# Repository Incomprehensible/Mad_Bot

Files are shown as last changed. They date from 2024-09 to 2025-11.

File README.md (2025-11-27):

# Mad_Bot
Exploratory project in Embedded Robotics and Swarm Algorithms

Warning: This is an ongoing project, and the repository is under construction!

## Features
* Small PCB-based frame, minimum 3D printed parts
* ESP32-S3 MCU with vector instructions, acceleration for neural network computing and signal processing workloads
* Wi-Fi, Bluetooth 5 and BLE connectivity
* Omnidirectional movement
* Quadrature encoders for precise movement
* 8 MB PSRAM for image processing
* 2 Megapixel camera and ToF sensors for running embedded robotics algorithms
* Powered via USB-C or 3000mAh LiPo battery with inner protection and external charging circuit
* Load sharing circuit for operating the robot while charging
* Buck-Boost converter for powering the MCU and peripherals
* 6V regulator for powering the middle power range motors
* ESPNOW, ESP-WIFI-MESH or ESP-BLE-MESH for communication between several robots
* Integrated MEMS microphone for sound recognition
* micro-ROS support

**Note**: Software support for some features is still in progress.

## Fusion360 design
| | |
|---|---|
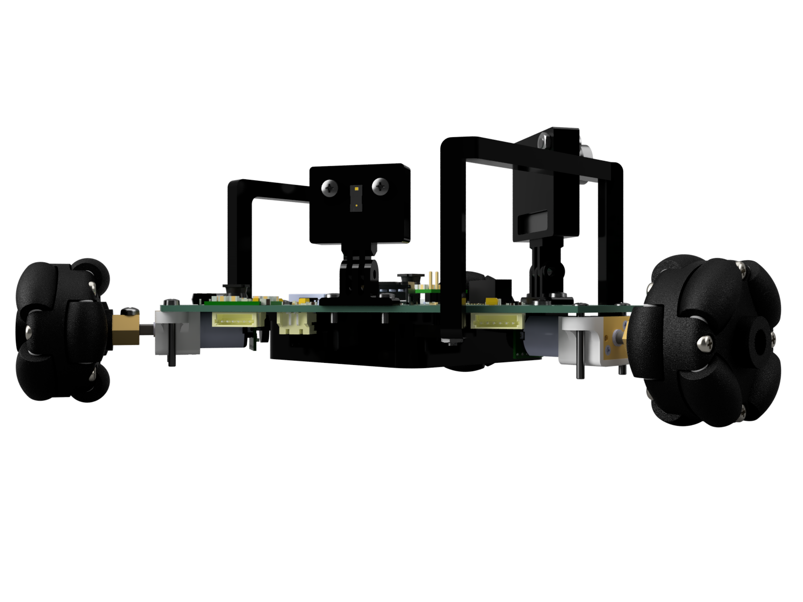
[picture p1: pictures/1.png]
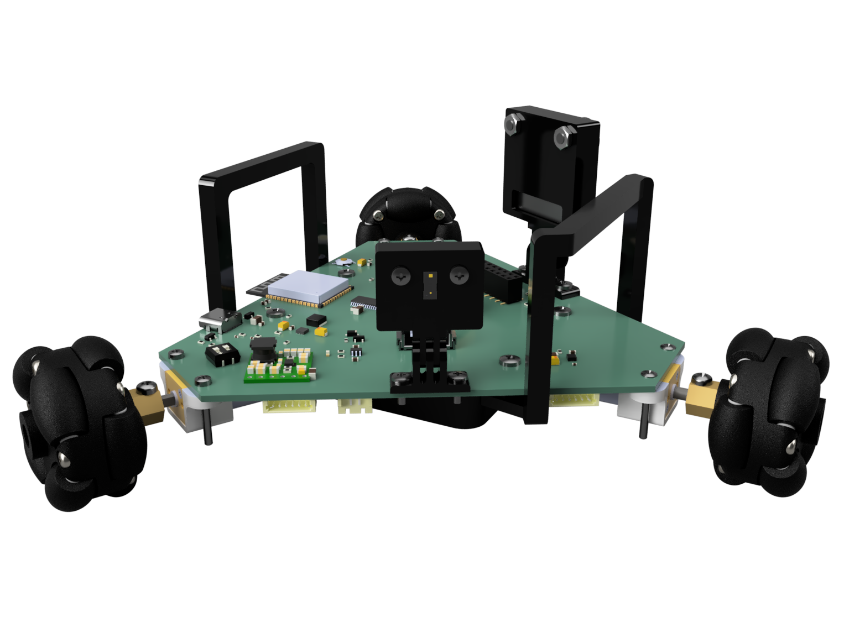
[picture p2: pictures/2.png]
|  |  |
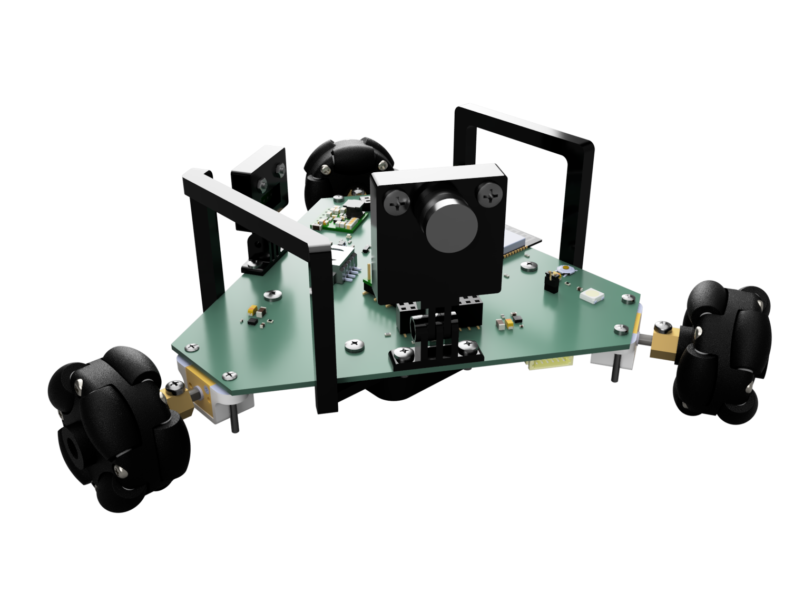
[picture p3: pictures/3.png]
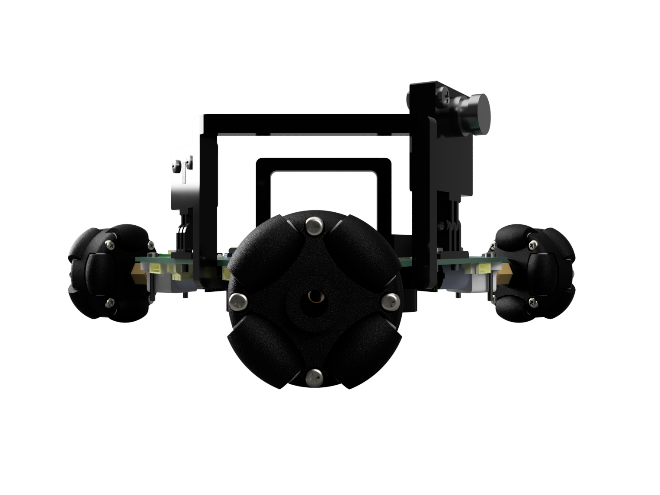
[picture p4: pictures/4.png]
|  |  |

## URDF model
<details>

| Robot | Wheel |
|---|---|
|  |  |

</details>

## Operation demo
<details>

| Forward movement | Backward movement | Rotation |
|:---:|:---:|:---:|
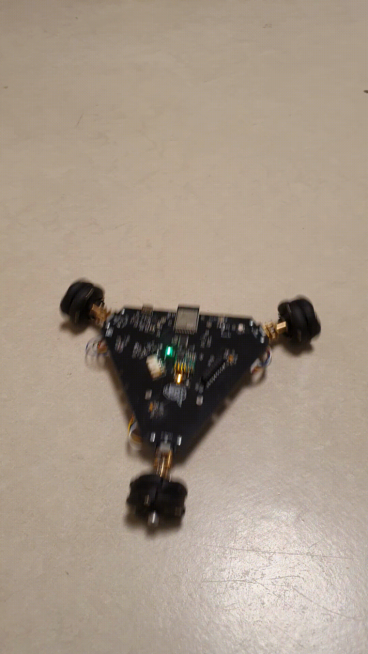
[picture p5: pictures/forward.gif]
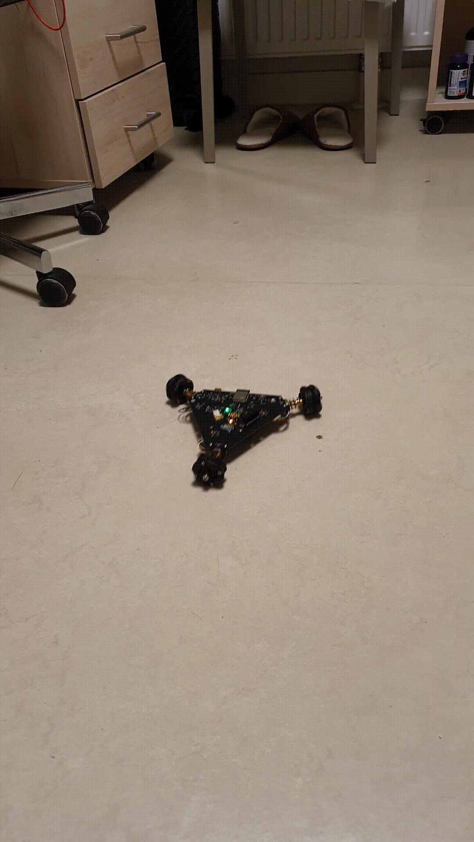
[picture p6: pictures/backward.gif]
|  |  |  |
<!-- | ![Forward movement](pictures/forward.gif) | ![Backward movement](pictures/backward.gif) | ![Rotation](pictures/twist.gif) | -->

</details>

### Charging mode
<details>
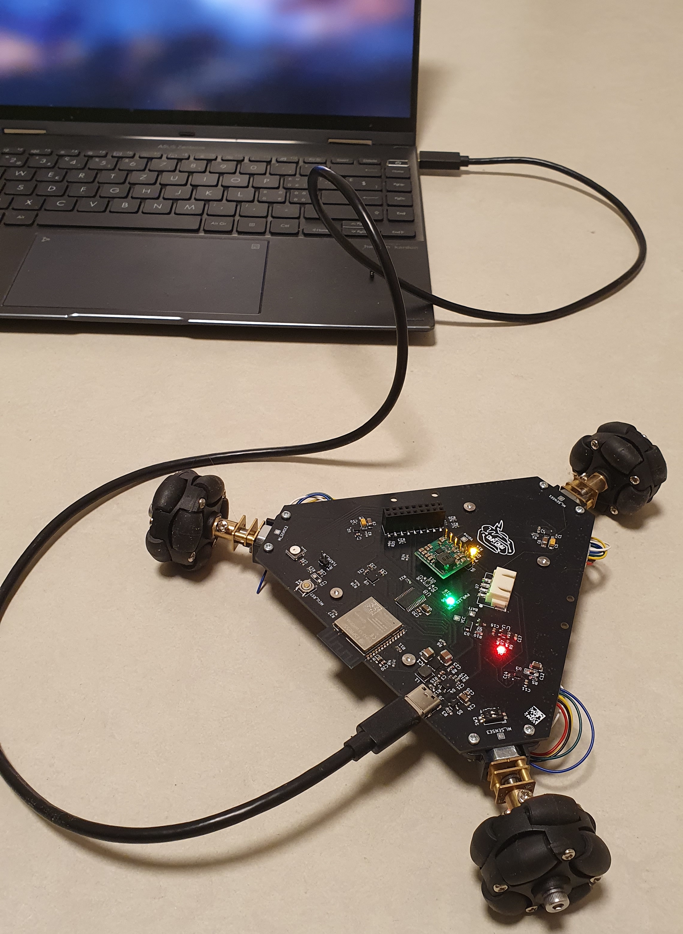
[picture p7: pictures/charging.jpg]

</details>

## Board layout
<details>

</details>

## Future work
- [ ] Add a BOM
- [X] Design a carrier extension in Fusion360
- [X] Test battery charging circuit
- [X] Test load sharing circuit
- [X] Test basic functionality with motors and ESP32-S3
- [X] Test Wi-Fi
- [X] Motors library (in progress)
- [X] Encoders testing
- [ ] **Device firmware (in progress)**
- [ ] **Sensors testing (in progress)**:
  - [ ] Camera
  - [X] ToF
  - [X] IMU
  - [ ] *MEMS microphone (requires PCB bug fix)*
- [ ] Remote controller based on ESP32
- [ ] PSRAM memory testing
- [X] **ROS2 integration via micro-ROS (in progress)**
- [ ] Web page with control interface and telemetry
- [X] URDF model
- [X] Joystick control via ROS2
- [ ] Digital twin for simulation in Gazebo and Mujoco
- [ ] ESPNOW and Mesh experiments
- [ ] Multi-agent algorithms
- [ ] Computer vision algorithms
- [ ] Mini SLAM experiments

## Fix list for new hardware revisions
* MEMS microphone footprint flipped
* Non-fixed Buck-Boost mentioned in the schematics instead of 3.3V fixed
* 6V regulator doesn't disconnect the load if disabled because of topology - extra switch needed
* Battery connector is hard to remove - source power switch needed
* Better (aligned) placement for camera & ToF sensors

## Software Troubleshooting

### micro-ROS build issues
If you encounter issue like [this](https://github.com/micro-ROS/micro_ros_espidf_component/issues/251) building micro-ROS for the ESP32-S3 platform, edit [`libmicroros.mk`](https://github.com/micro-ROS/micro_ros_espidf_component/blob/humble/libmicroros.mk) file at line 110 to include `esp32s3` as follows:

```makefile
ifeq ($(IDF_TARGET),$(filter $(IDF_TARGET),esp32s2 esp32c3 esp32c6 esp32s3))
```

## Acknowledgements
This project takes inspiration from the following open-source projects:
* https://github.com/YePeOn7/ros2_omni_robot_sim (omnidirectional drive kinematics)
* https://github.com/twistx77/V53L7CX-Library.git (ToF sensor library)
* https://github.com/natanaeljr/esp32-mpu-driver (IMU driver)
* Jonas Scharpf code pf the PCA9685 driver (motor PWM driver)

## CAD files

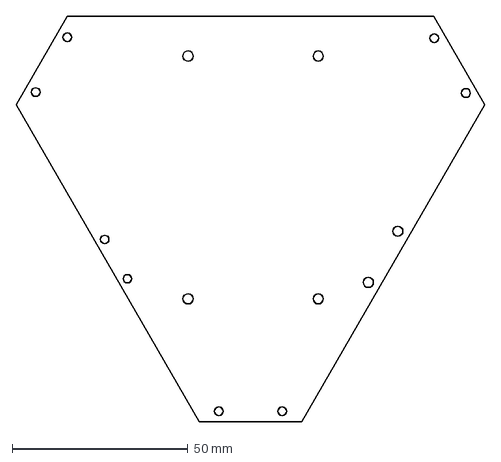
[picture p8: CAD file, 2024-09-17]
pcb_design/Board Outline.dxf
133.1 x 115.3 mm

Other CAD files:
3d_models/ESP32-S3-WROOM-1-N8R8.step
fusion360/PCB.step
urdf/meshes/roller2.stl
3d_models/step-up-voltage-regulator-u3v40fx.step
fusion360/Mad_Bot.step
urdf/meshes/wheel_fixture2-2.stl
3d_models/IC12_MP6550_MNP.step
urdf/meshes/roller1-1.stl
3d_models/QFN24_3X3X0P9_MPU6500.step
urdf/meshes/root1.stl
3d_models/PCA9685PW_118.step
urdf/meshes/roller6.stl
3d_models/TYPE-C-31-M-12.step
urdf/meshes/roller5-1.stl
3d_models/MPU-6500.step
urdf/meshes/Component42.stl
3d_models/TYPE-C-31-M-12-ver2.step
3d_models/AO3400A--3DModel-STEP-269445.STEP
3d_models/HRO_TYPE-C-31-M-12.step
3d_models/Jumper-2mm-h3.5.STEP
3d_models/MCP73831T-2ACI_OT.step
3d_models/PTS526_SK15_SMTR2_LFS.stp
3d_models/RT6150BGQW.stp
3d_models/S2B-PH-SM4-TB_LF__SN_.step
3d_models/S4B-XH-SM4-TB-LF--SN---3DModel-STEP-56544.STEP
3d_models/S6B-ZR-SM4A-TF_1.5mm.step
3d_models/WS2812B.step
fusion360/Mad_Bot.f3z
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

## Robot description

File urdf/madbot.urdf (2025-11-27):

<?xml version='1.0' encoding='utf-8'?>
<robot name="madbot">
    <link name="roller8">
        <inertial>
            <origin xyz="1.0439394522909762e-06 -1.4014728133560085e-09 4.298914557665512e-09" rpy="0.0 -0.0 0.0" />
            <mass value="0.007815431237643264" />
            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
        </inertial>
        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
    </link>
    <link name="root1">
        <inertial>
            <origin xyz="-3.100341341877311e-08 -1.1752218942007176e-07 1.1202703679824566e-07" rpy="0.0 1.5407439555097882e-33 0.0" />
            <mass value="0.0004307740437553794" />
            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
        </inertial>
        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
    </link>
    <link name="roller2">
        <inertial>
            <origin xyz="7.104420888293106e-07 7.407909580248173e-07 1.9459895433726615e-07" rpy="0.0 -1.8662408846864425e-43 0.0" />
            <mass value="0.007815431237643047" />
            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
        </inertial>
        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
    </link>
    <link name="stem1">
        <inertial>
            <origin xyz="1.8899693657381533e-06 7.304546818021063e-06 -7.0571409794828455e-06" rpy="0.0 1.540743955510633e-33 0.0" />
            <mass value="0.0011510552143977049" />
            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
        </inertial>
        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
    </link>
    <link name="roller1">
        <inertial>
            <origin xyz="-1.905487767572822e-07 -7.385234957646425e-07 7.177578375516803e-07" rpy="0.0 -2.77207726435891e-43 1.4349296274686127e-42" />
            <mass value="0.007815431237643685" />
            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
        </inertial>
        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
    </link>
    <link name="stem2">
        <inertial>
            <origin xyz="-7.057385601761945e-06 -7.3022794153221325e-06 -1.8929902407727184e-06" rpy="0.0 -1.5407439555079787e-33 -6.162975822039155e-33" />
            <mass value="0.0011510552143976025" />
            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
        </inertial>
        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
    </link>
    <link name="root3">
        <inertial>
            <origin xyz="2.71807154028636e-08 -1.1371580499686118e-07 1.1118542941224164e-07" rpy="0.0 -1.5407439555097882e-33 -6.162975822039155e-33" />
            <mass value="0.00043077404375536606" />
            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
        </inertial>
        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
    </link>
    <link name="root4">
        <inertial>
            <origin xyz="-1.1801200489269803e-07 1.1359585382231252e-07 3.123094604262633e-08" rpy="0.0 1.5407439555097883e-33 0.0" />
            <mass value="0.00043077404375537924" />
            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
        </inertial>
        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
    </link>
    <link name="stem5">
        <inertial>
            <origin xyz="-5.165218458689225e-06 1.4776153689499694e-09 8.945080346620672e-06" rpy="0.0 -0.0 0.0" />
            <mass value="0.001151055214397071" />
            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
        </inertial>
        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
    </link>
    <link name="roller5">
        <inertial>
            <origin xyz="-3.137685427709869e-06 1.477901773183632e-09 5.437748869319137e-06" rpy="0.0 -0.0 0.0" />
            <mass value="0.00781543123764419" />
            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
        </inertial>
        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
    </link>
    <link name="Component14">
        <inertial>
            <origin xyz="0.0002571060522190471 0.00014897032367631625 -5.603945090504325e-07" rpy="0.0 -0.0 0.0" />
            <mass value="0.0004109447446555896" />
            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
        </inertial>
        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
    </link>
    <link name="Component15">
        <inertial>
            <origin xyz="0.0002571112578287682 0.00014897302145918444 -5.590028332258523e-07" rpy="0.0 -0.0 0.0" />
            <mass value="0.00041094474463731237" />
            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
        </inertial>
        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
    </link>
    <link name="roller7">
        <inertial>
            <origin xyz="-5.219318596960676e-07 1.4772004419683072e-09 -9.074879243442524e-07" rpy="0.0 8.758115402067066e-47 0.0" />
            <mass value="0.007815431237643496" />
            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
        </inertial>
        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
    </link>
    <link name="Component17">
        <inertial>
            <origin xyz="0.00025706019450405293 0.00014905965433701596 4.6687570287029526e-07" rpy="0.0 -0.0 0.0" />
            <mass value="0.00041094474463718855" />
            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
        </inertial>
        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
    </link>
    <link name="roller6">
        <inertial>
            <origin xyz="-1.0439387513150322e-06 -3.405877295747928e-09 4.2235343933327844e-09" rpy="4.307493387644509e-59 -0.0 0.0" />
            <mass value="0.007815431237643378" />
            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
        </inertial>
        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
    </link>
    <link name="stem6">
        <inertial>
            <origin xyz="-1.4214342886342823e-06 -3.40612094085202e-09 4.2236750541491124e-09" rpy="4.307493387644509e-59 -0.0 0.0" />
            <mass value="0.0011510552143977034" />
            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
        </inertial>
        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
    </link>
    <link name="root2">
        <inertial>
            <origin xyz="1.1178253624954949e-07 1.197894636328911e-07 2.7982571122464605e-08" rpy="0.0 -1.5407439555097883e-33 0.0" />
            <mass value="0.00043077404375539203" />
            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
        </inertial>
        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
    </link>
    <link name="roller4">
        <inertial>
            <origin xyz="-7.096004910112086e-07 7.345973547984164e-07 1.9077625985630677e-07" rpy="0.0 -1.600695501510992e-51 0.0" />
            <mass value="0.007815431237643463" />
            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
        </inertial>
        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
    </link>
    <link name="stem7">
        <inertial>
            <origin xyz="-7.106796283640193e-07 1.476918787268744e-09 -1.2344086490578832e-06" rpy="0.0 8.758115402067066e-47 0.0" />
            <mass value="0.0011510552143978619" />
            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
        </inertial>
        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
    </link>
    <link name="stem4">
        <inertial>
            <origin xyz="7.051156133495162e-06 -7.308473026466089e-06 -1.8897418681795843e-06" rpy="0.0 1.5407439555101537e-33 -6.162975822039155e-33" />
            <mass value="0.0011510552143976602" />
            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
        </inertial>
        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
    </link>
    <link name="root7">
        <inertial>
            <origin xyz="-8.290144054790005e-08 1.476955353574283e-09 -1.4706493130844934e-07" rpy="0.0 -0.0 0.0" />
            <mass value="0.0004307740437555343" />
            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
        </inertial>
        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
    </link>
    <link name="roller3">
        <inertial>
            <origin xyz="1.937971468102262e-07 -7.347171158672561e-07 7.09845161466216e-07" rpy="0.0 -4.3302330459644565e-45 0.0" />
            <mass value="0.007815431237643299" />
            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
        </inertial>
        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
    </link>
    <link name="root5">
        <inertial>
            <origin xyz="8.297682004609897e-08 1.4776574397412645e-09 -1.4506052782081723e-07" rpy="0.0 -0.0 0.0" />
            <mass value="0.00043077404375551774" />
            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
        </inertial>
        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
    </link>
    <link name="stem3">
        <inertial>
            <origin xyz="-1.893792061284927e-06 7.308353204705797e-06 -7.057982583879019e-06" rpy="1.751623080406021e-46 6.211560498438912e-60 -7.006492321624084e-46" />
            <mass value="0.0011510552143976153" />
            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
        </inertial>
        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
    </link>
    <link name="root6">
        <inertial>
            <origin xyz="-1.6587791243027894e-07 -3.406091675373091e-09 4.223658214286274e-09" rpy="-3.038581678643135e-64 -0.0 0.0" />
            <mass value="0.0004307740437553726" />
            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
        </inertial>
        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
    </link>
    <link name="Component29">
        <inertial>
            <origin xyz="-0.002595641529595074 0.0014985139369473545 -7.228449571705653e-07" rpy="0.0 -0.0 0.0" />
            <mass value="0.0004109447446236162" />
            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
        </inertial>
        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
    </link>
    <link name="Component30">
        <inertial>
            <origin xyz="-0.00025770289094363187 0.00014795231939298325 6.769750041046851e-08" rpy="0.0 -0.0 0.0" />
            <mass value="0.000410944743236442" />
            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
        </inertial>
        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
    </link>
    <link name="Component31">
        <inertial>
            <origin xyz="0.0002576191973983555 0.000148093341563591 -4.6687677290657703e-07" rpy="0.0 -0.0 0.0" />
            <mass value="0.00041094474465542847" />
            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
        </inertial>
        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
    </link>
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

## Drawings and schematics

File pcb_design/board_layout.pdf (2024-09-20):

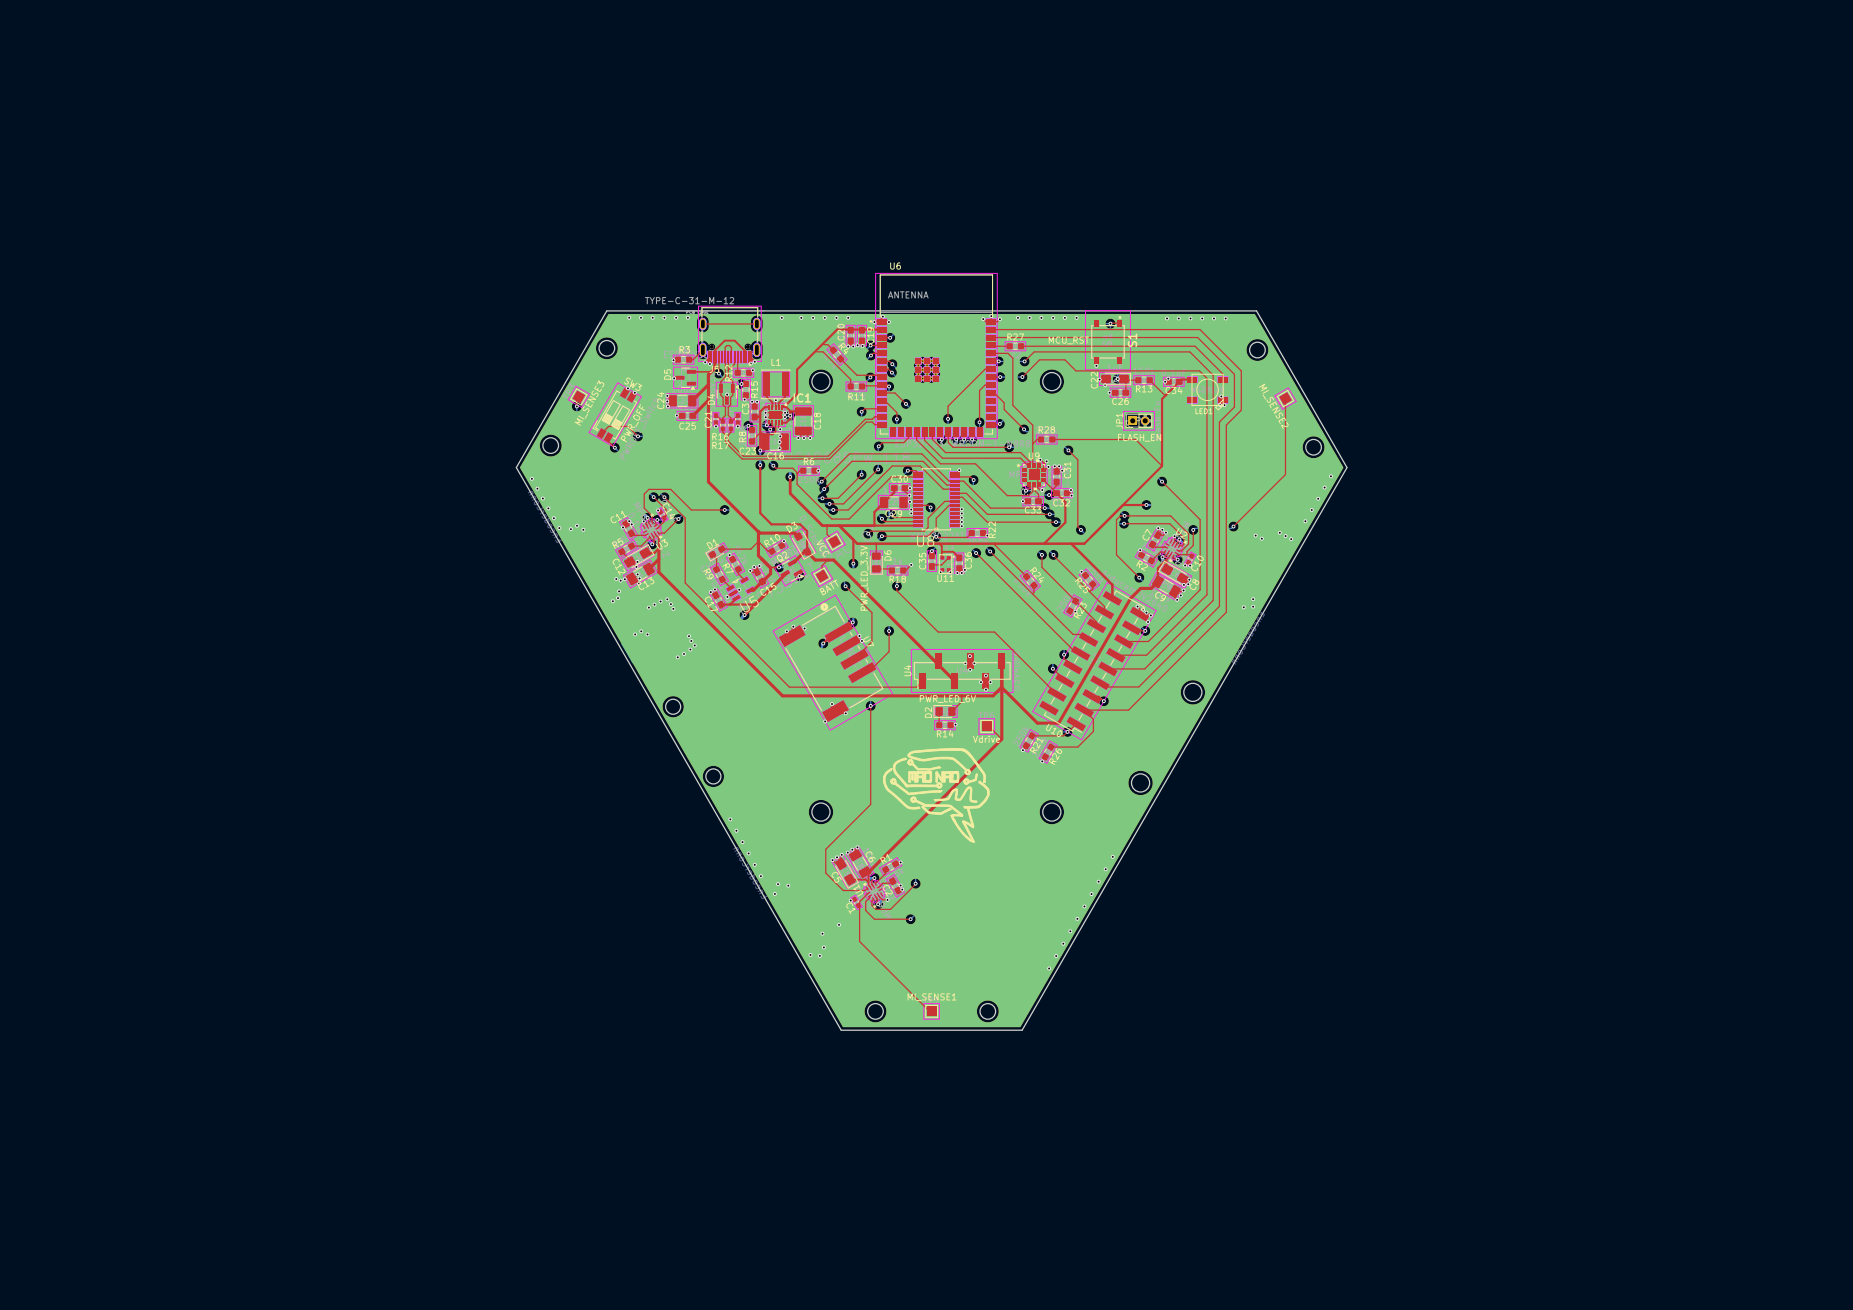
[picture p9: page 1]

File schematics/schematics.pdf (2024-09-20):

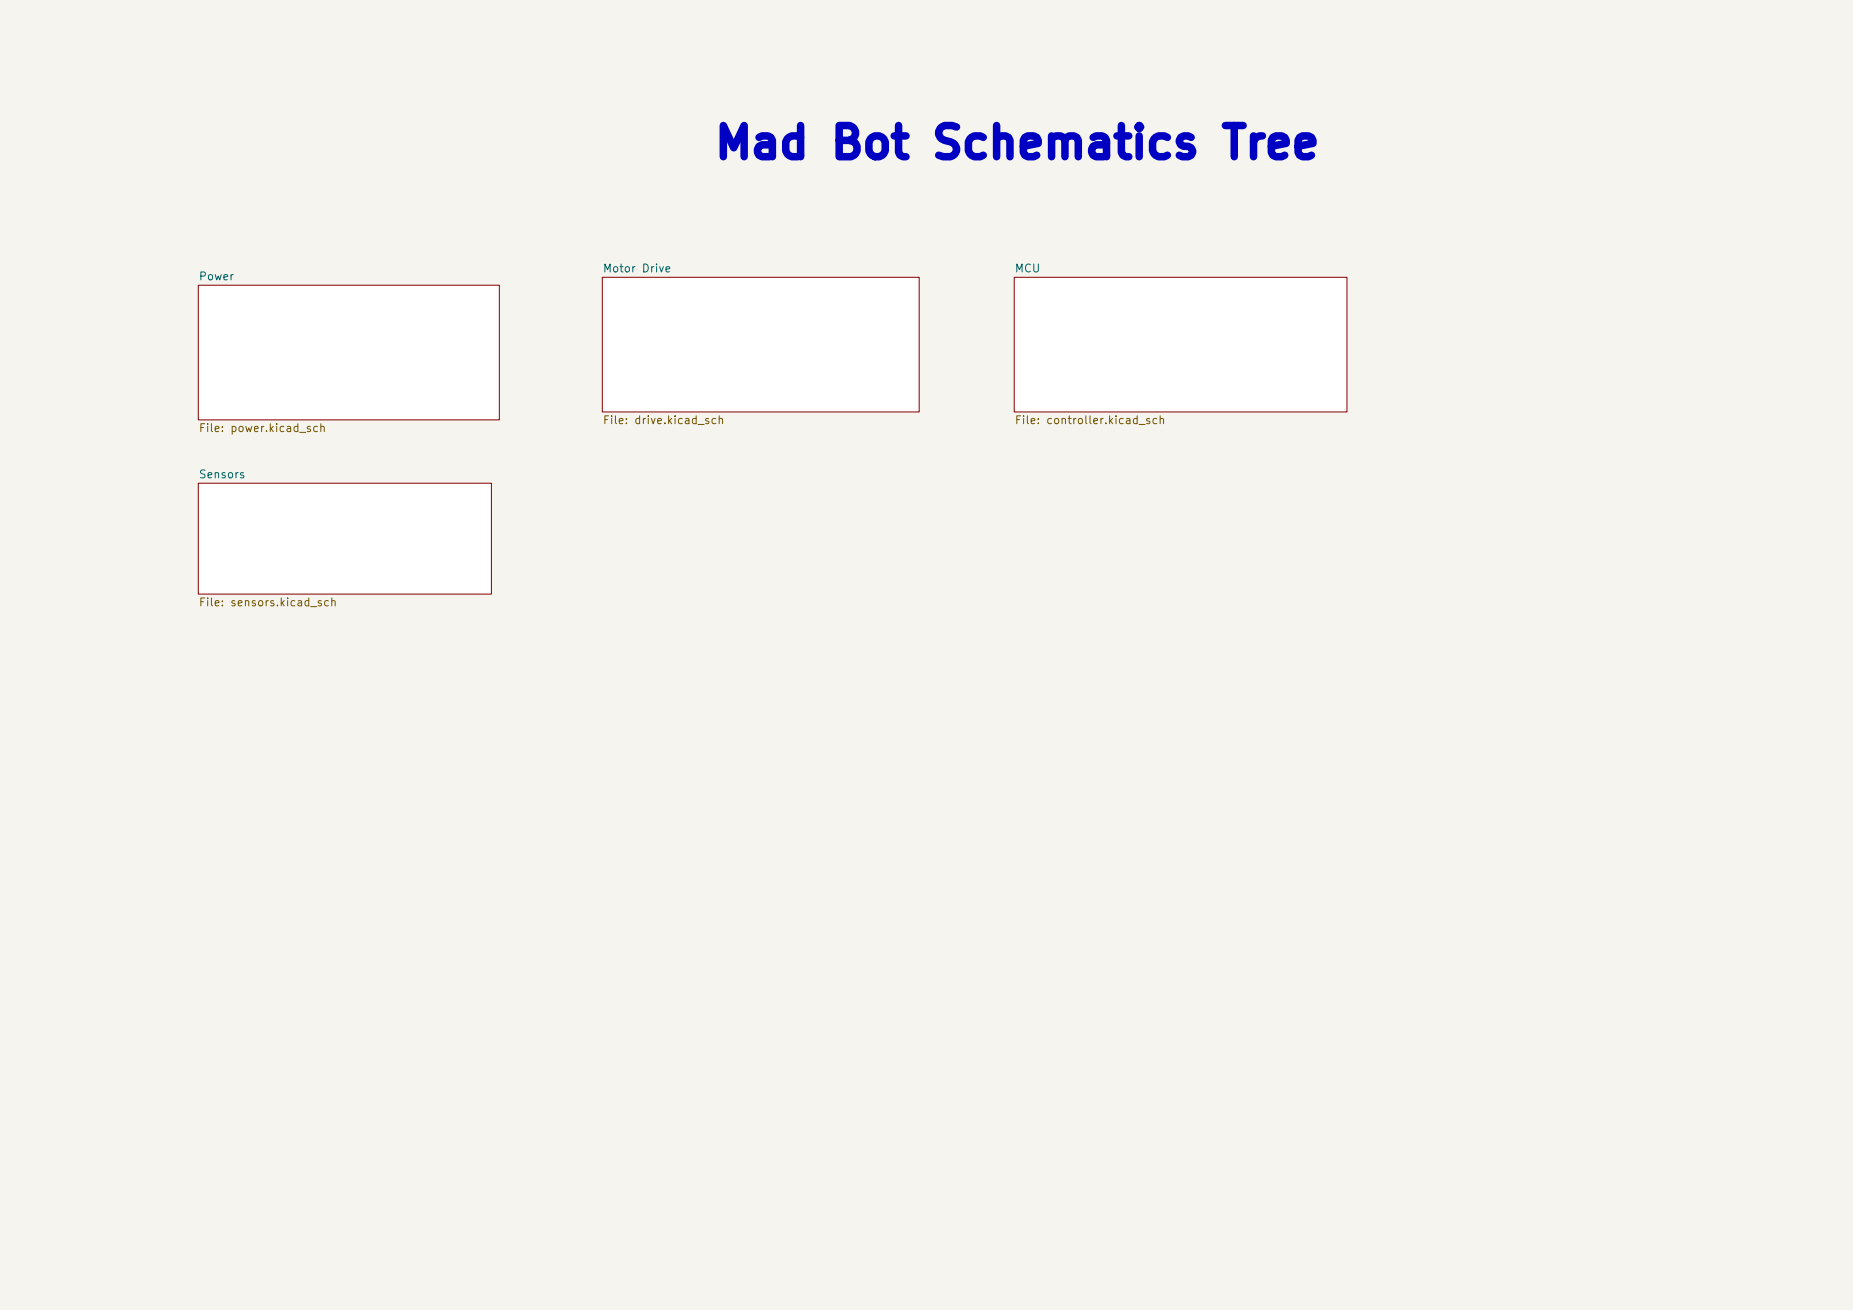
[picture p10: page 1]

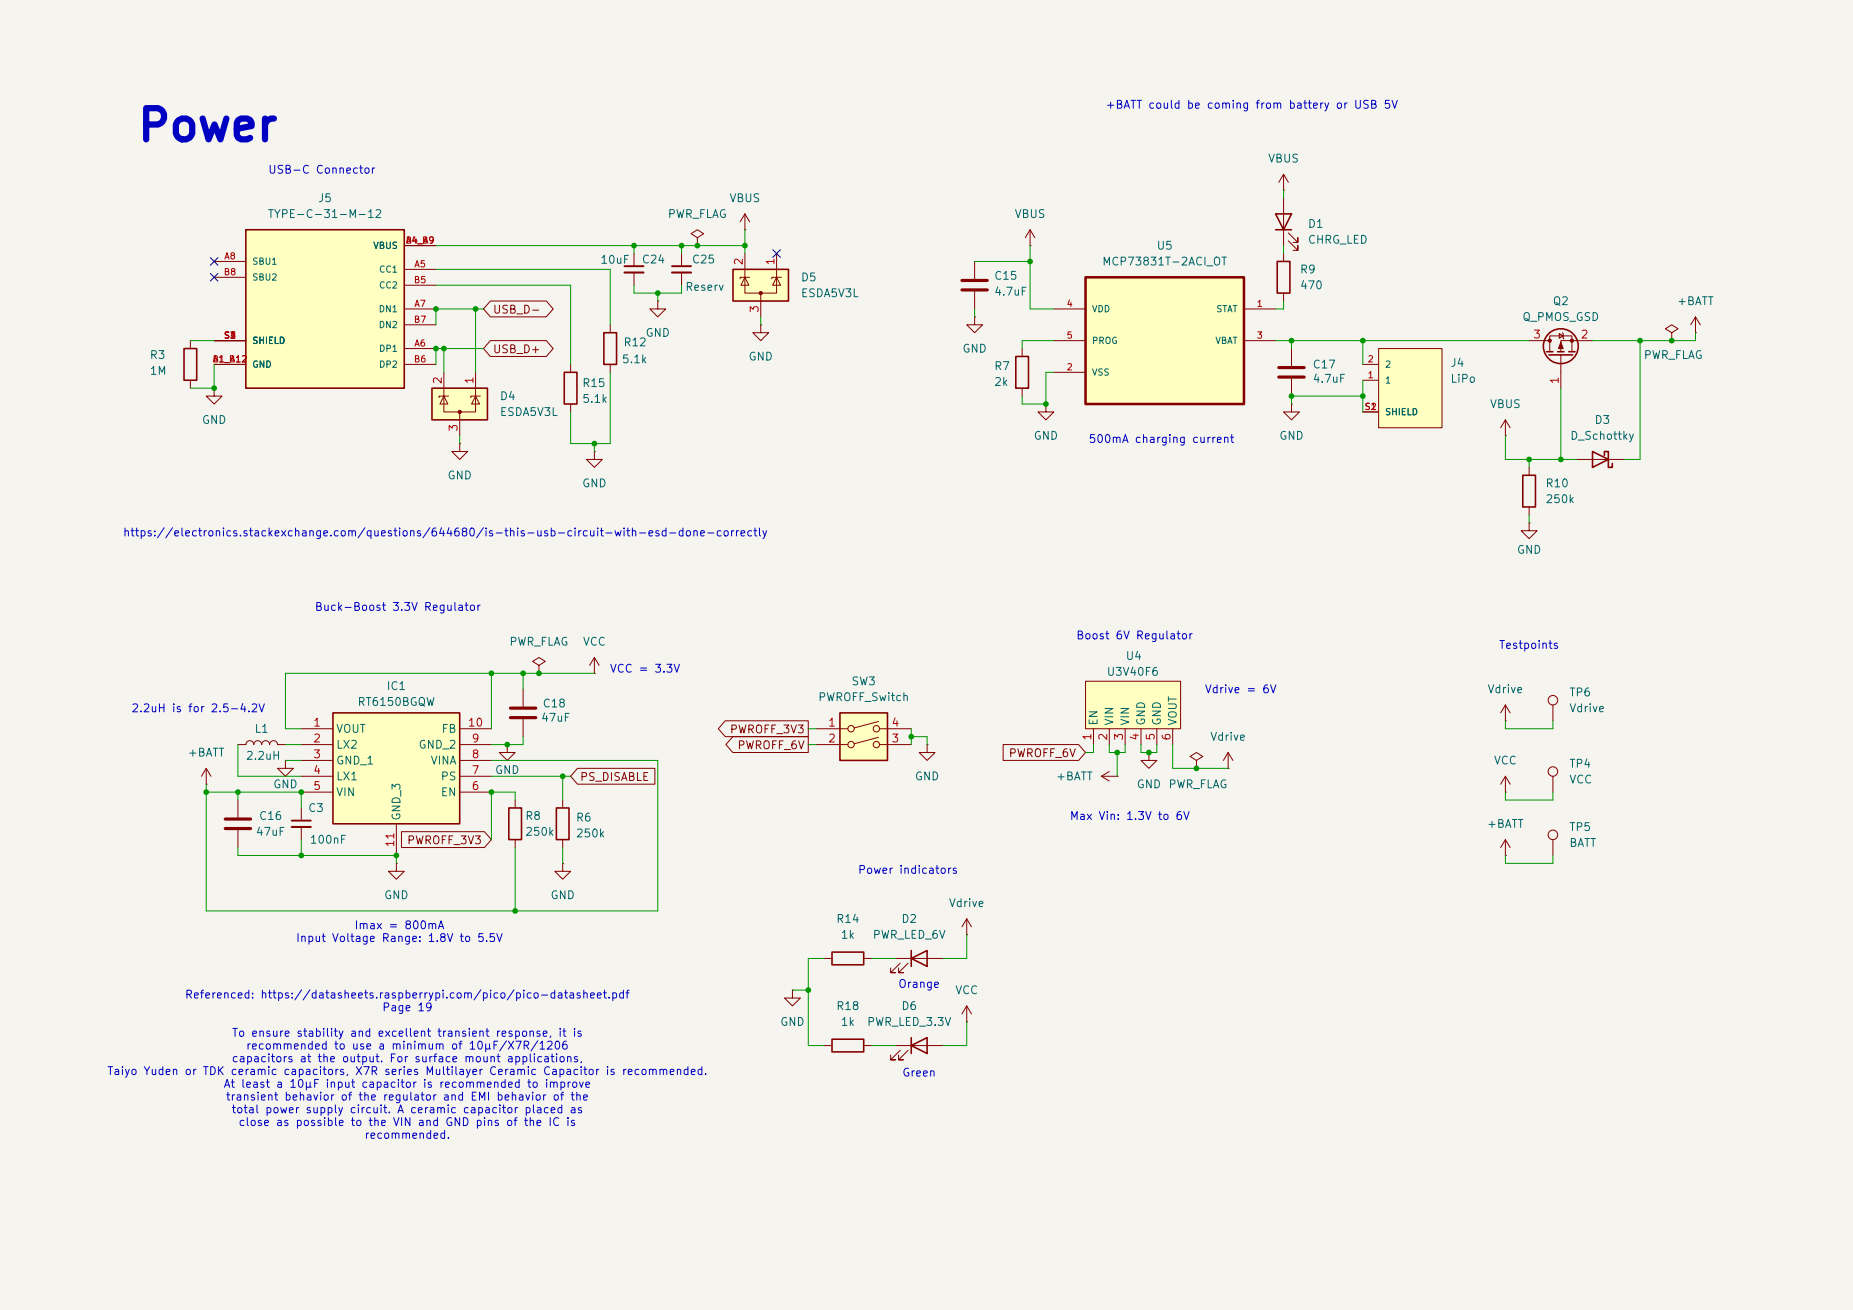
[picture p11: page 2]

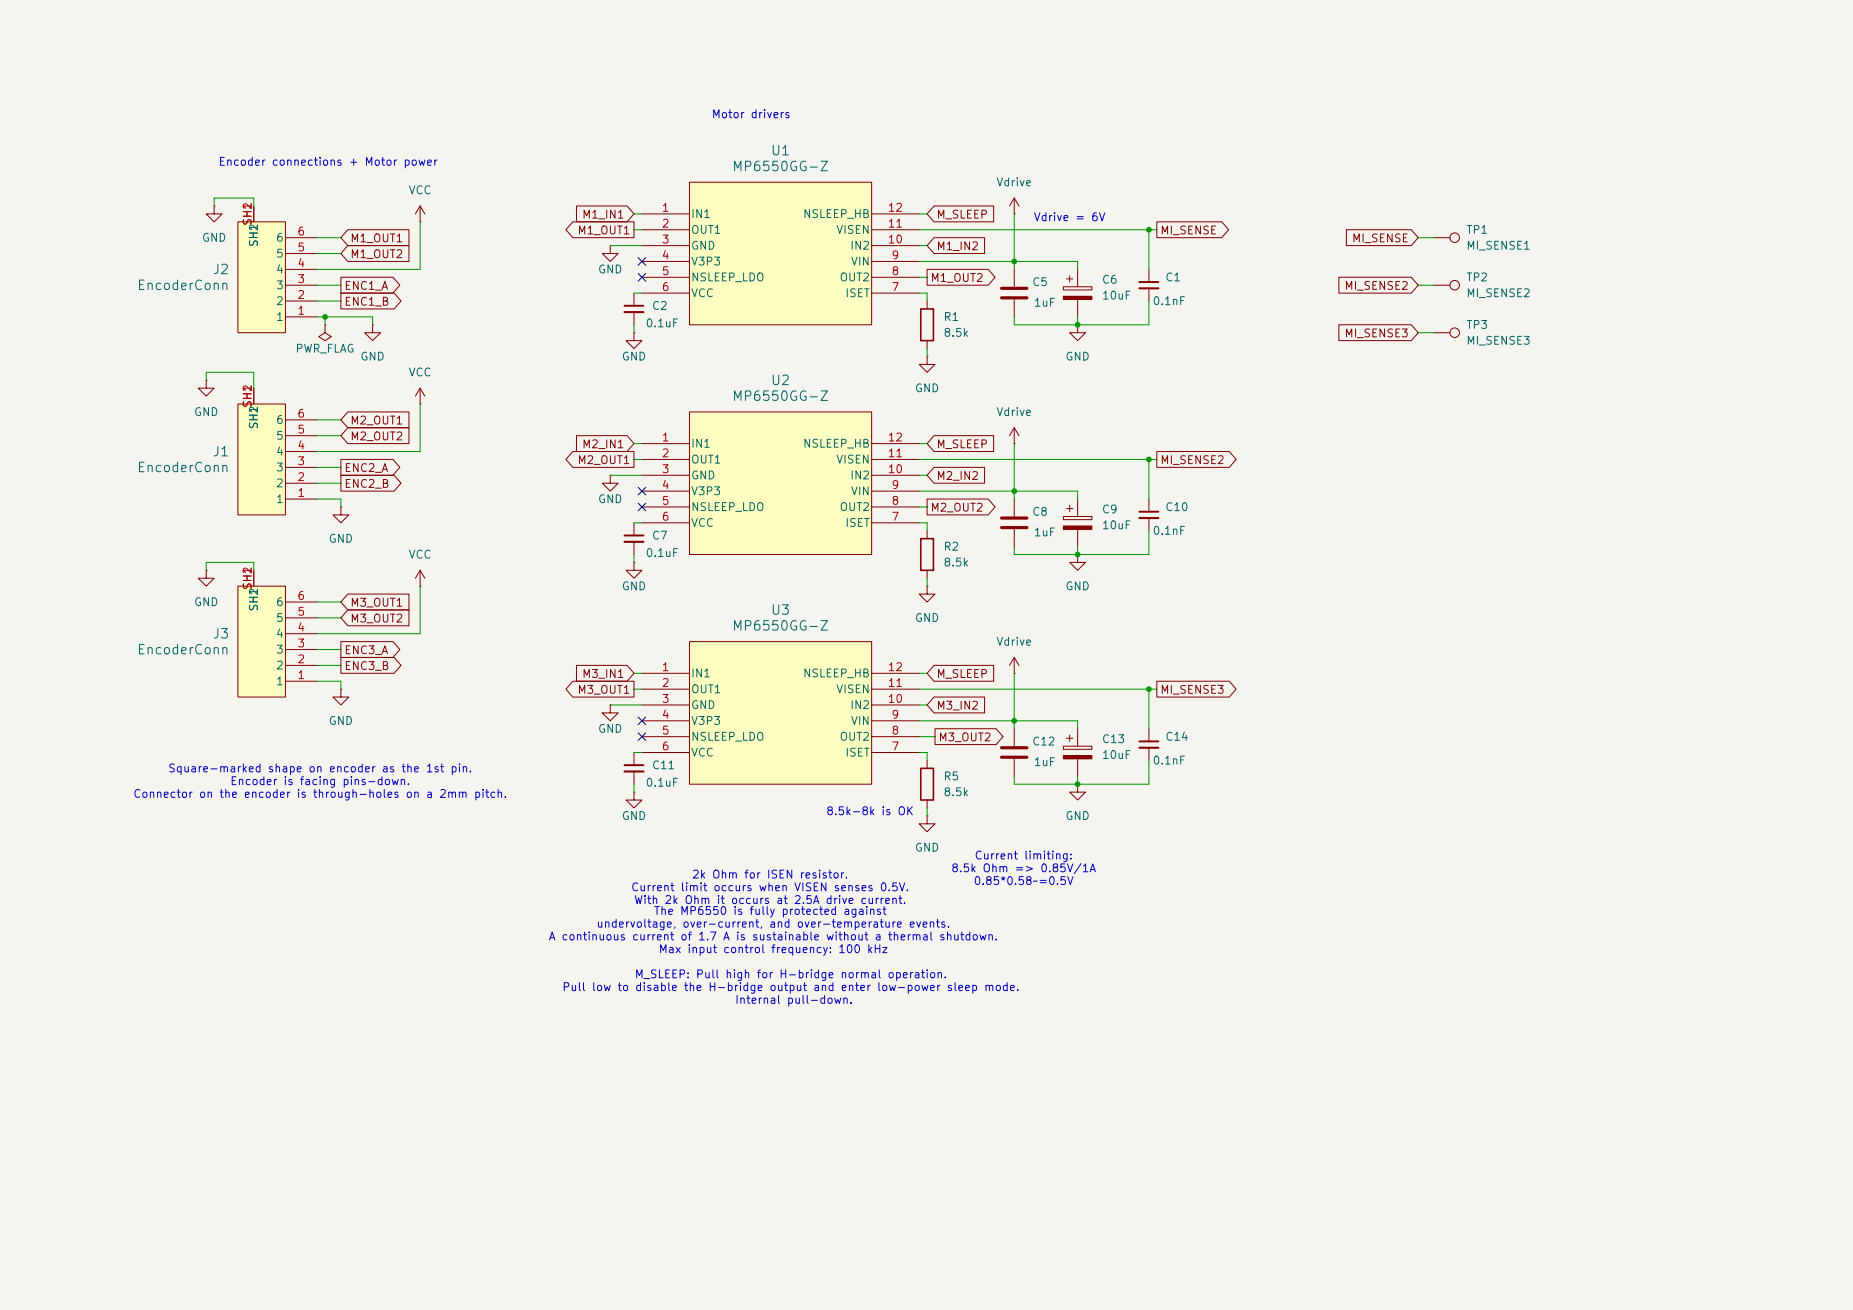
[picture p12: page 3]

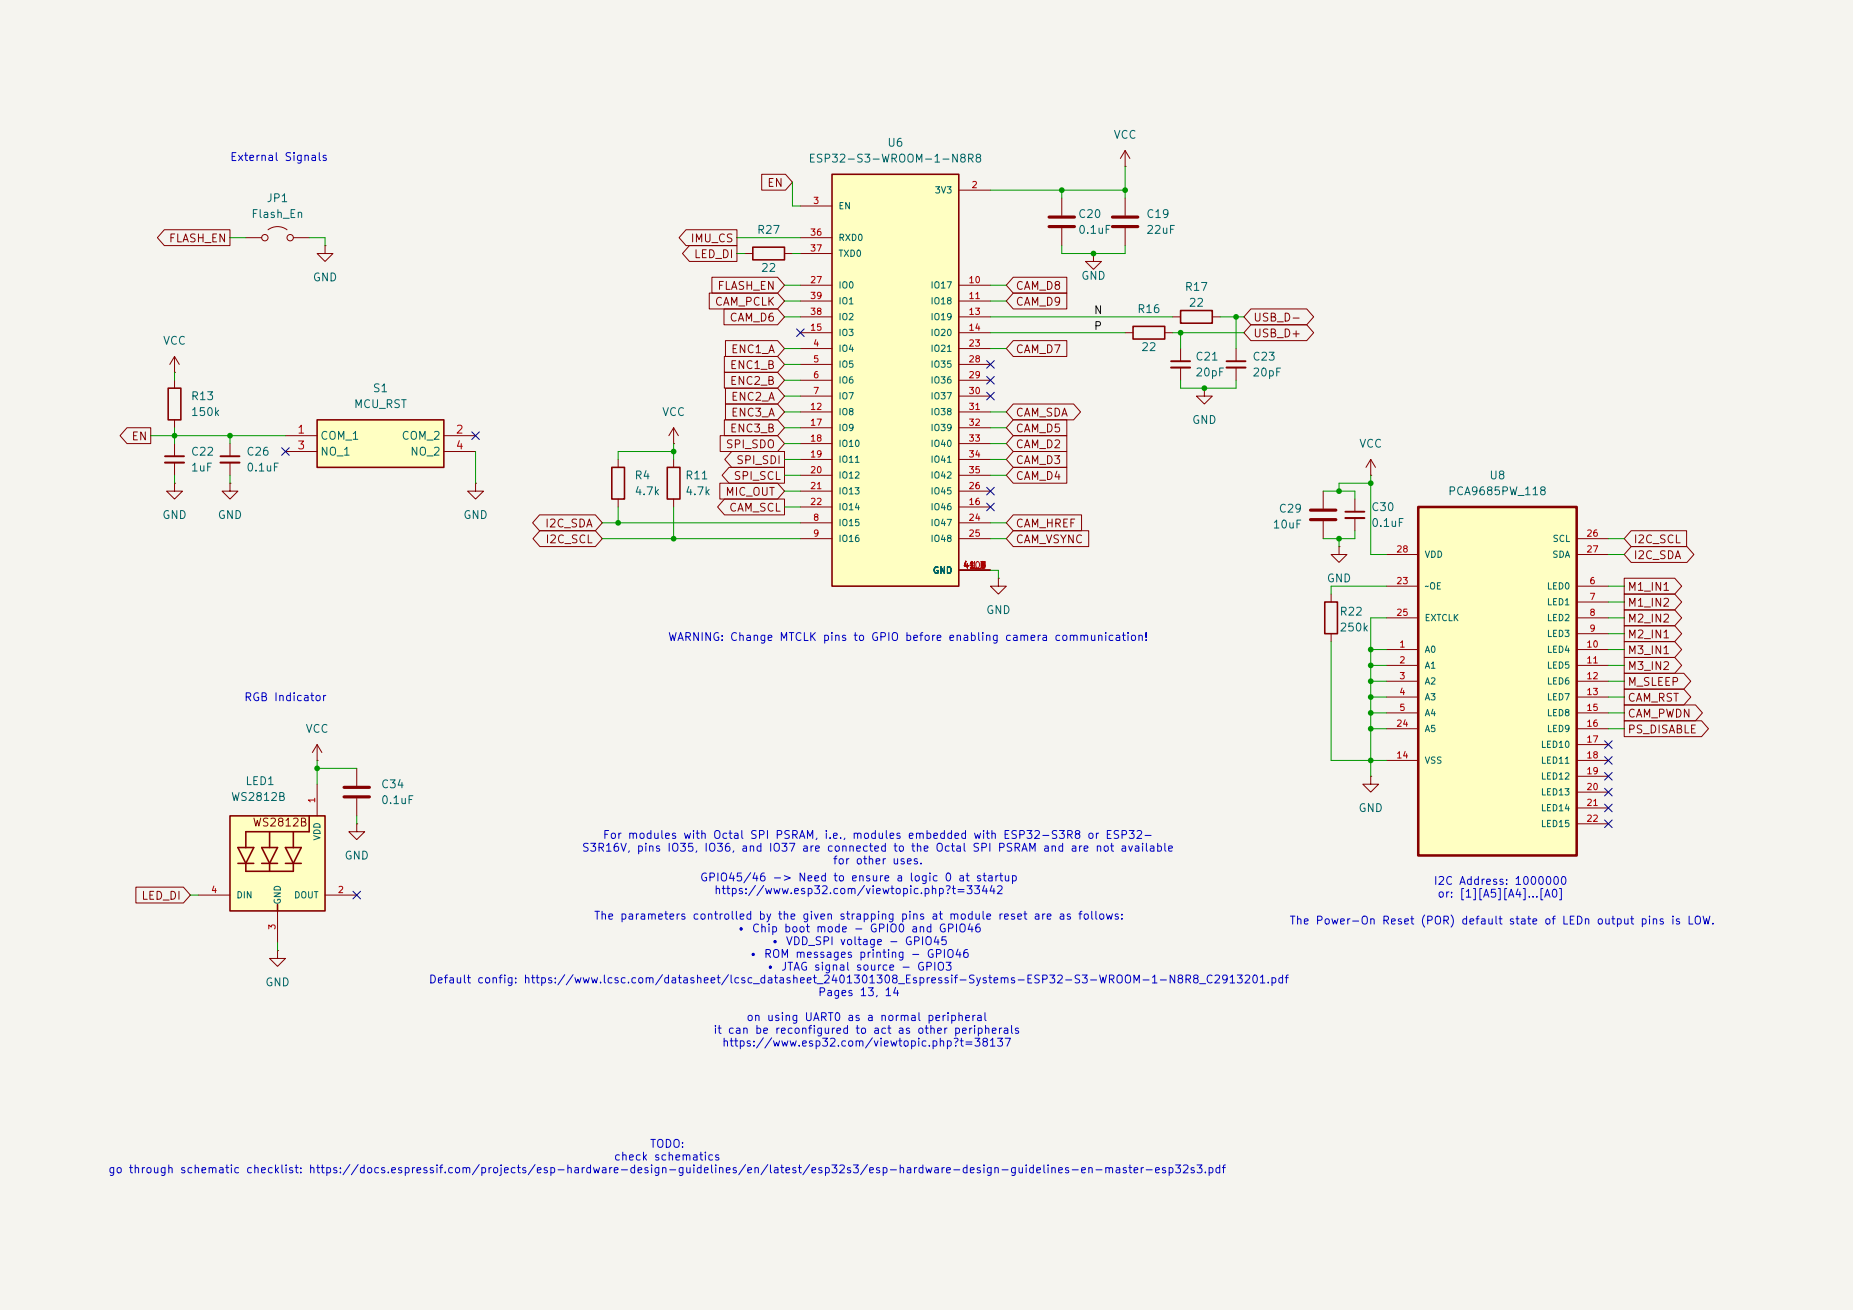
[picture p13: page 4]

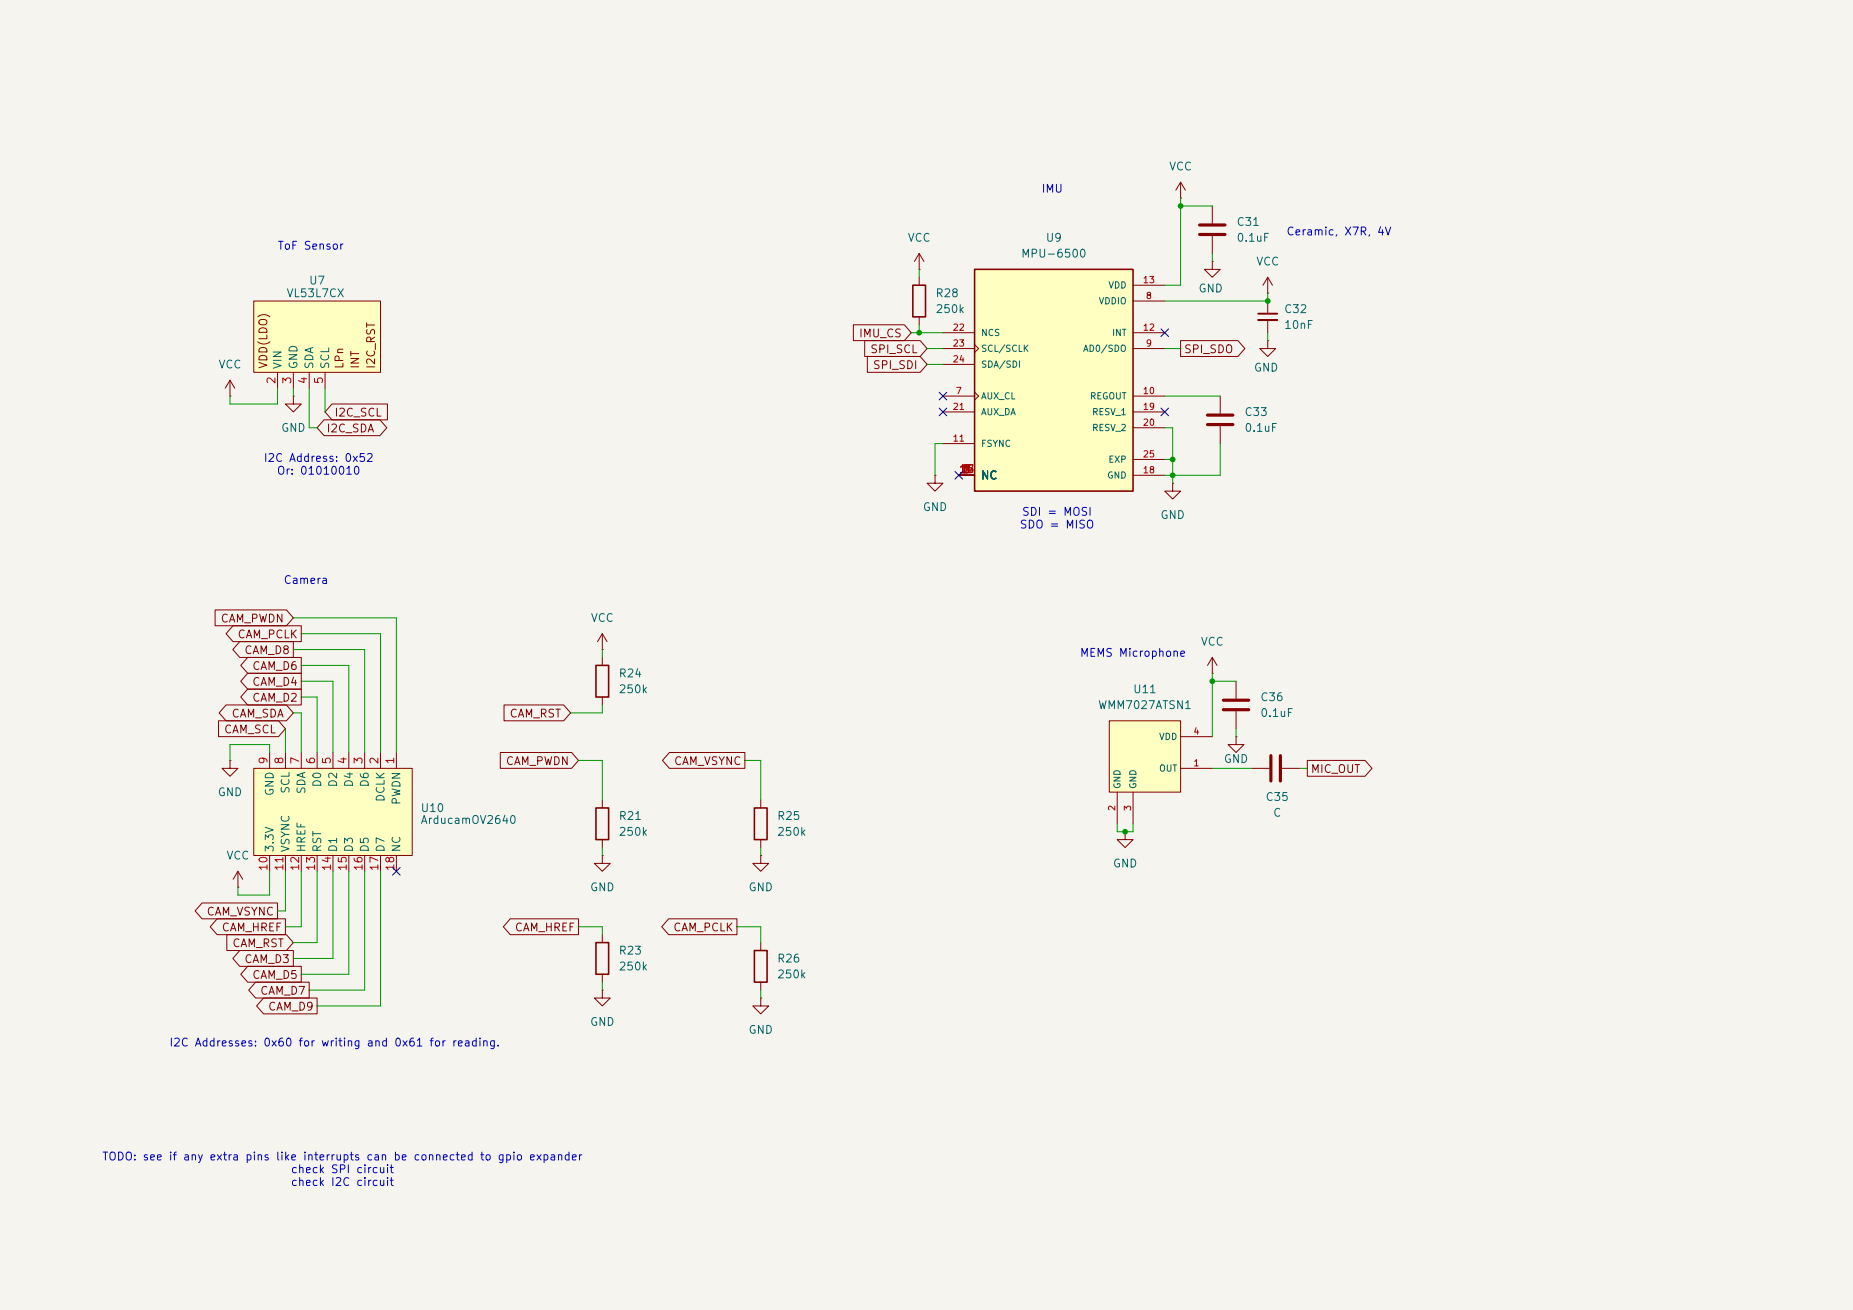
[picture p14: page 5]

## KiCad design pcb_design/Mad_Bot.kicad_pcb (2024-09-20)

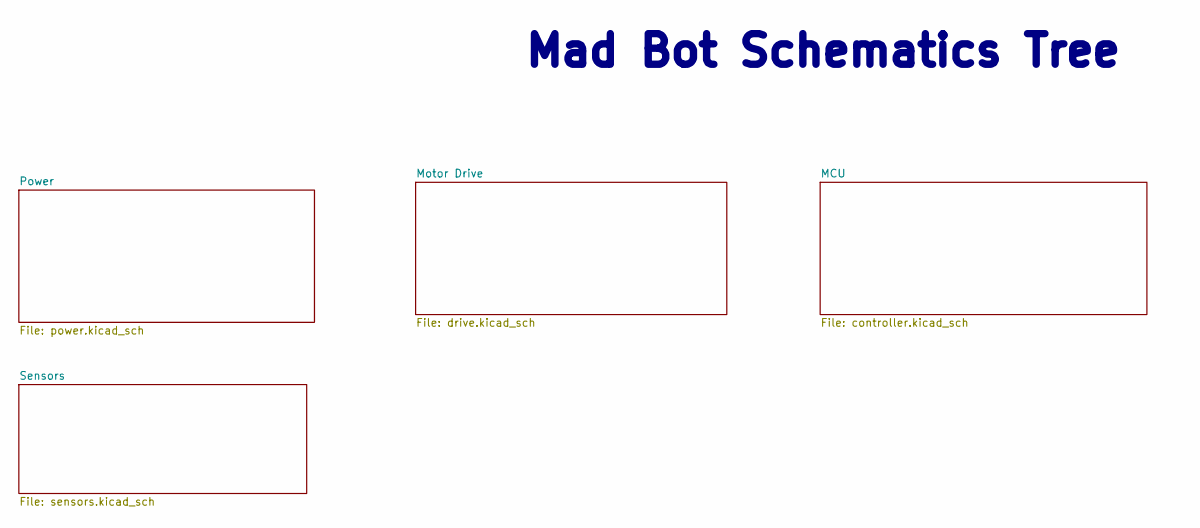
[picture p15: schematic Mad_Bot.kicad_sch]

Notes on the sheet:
Mad Bot Schematics Tree

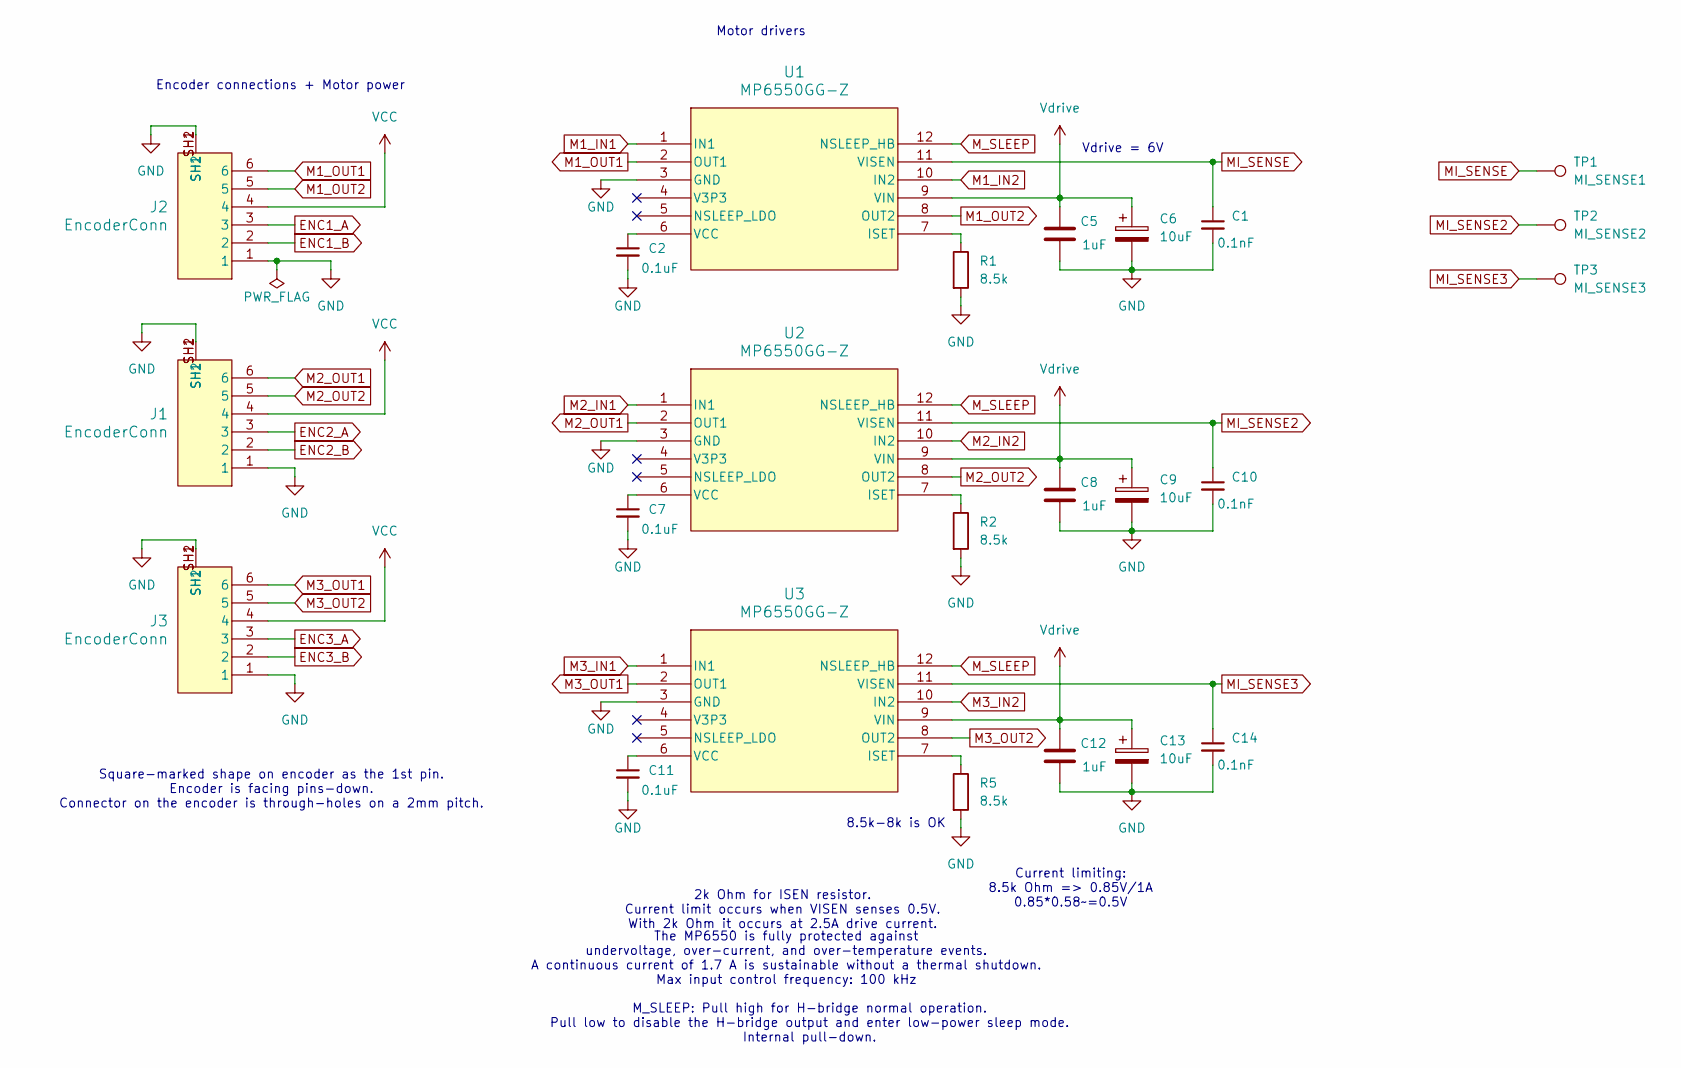
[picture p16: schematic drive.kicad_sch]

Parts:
C1, C10, C14: 0.1nF; C_0402_1005Metric_Pad0.74x0.62mm_HandSolder
C2, C7, C11: 0.1uF; C_0603_1608Metric_Pad1.08x0.95mm_HandSolder
C5, C8, C12: 1uF; CP_EIA-3216-18_Kemet-A_Pad1.58x1.35mm_HandSolder
C6, C9, C13: 10uF; C_1206_3216Metric_Pad1.33x1.80mm_HandSolder
J1, J2, J3: EncoderConn; JST_S6B-ZR-SM4A-TF_1.5mm
R1, R2, R5: 8.5k; R_0603_1608Metric_Pad0.98x0.95mm_HandSolder
TP1: MI_SENSE1; TestPoint_Pad_1.5x1.5mm
TP2: MI_SENSE2; TestPoint_Pad_1.5x1.5mm
TP3: MI_SENSE3; TestPoint_Pad_1.5x1.5mm
U1, U2, U3: MP6550GG-Z; IC12_MP6550_MNP

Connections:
ENC1_A: J2.3; also elsewhere on the board
ENC1_B: J2.2; also elsewhere on the board
ENC2_A: J1.3; also elsewhere on the board
ENC2_B: J1.2; also elsewhere on the board
ENC3_A: J3.3; also elsewhere on the board
ENC3_B: J3.2; also elsewhere on the board
GND: C1.2, C2.2, C5.2, C6.2, C7.2, C8.2, C9.2, C10.2, C11.2, C12.2, C13.2, C14.2, J1.1, J1.SH1, J1.SH2, J2.1, J2.SH1, J2.SH2, J3.1, J3.SH1, J3.SH2, R1.2, R2.2, R5.2, U1.3 (GND), U2.3 (GND), U3.3 (GND); also elsewhere on the board
M1_IN1: U1.1 (IN1); also elsewhere on the board
M1_IN2: U1.10 (IN2); also elsewhere on the board
M1_OUT1: J2.6, U1.2 (OUT1)
M1_OUT2: J2.5, U1.8 (OUT2)
M2_IN1: U2.1 (IN1); also elsewhere on the board
M2_IN2: U2.10 (IN2); also elsewhere on the board
M2_OUT1: J1.6, U2.2 (OUT1)
M2_OUT2: J1.5, U2.8 (OUT2)
M3_IN1: U3.1 (IN1); also elsewhere on the board
M3_IN2: U3.10 (IN2); also elsewhere on the board
M3_OUT1: J3.6, U3.2 (OUT1)
M3_OUT2: J3.5, U3.8 (OUT2)
MI_SENSE: C1.1, TP1.1, U1.11 (VISEN)
MI_SENSE2: C10.1, TP2.1, U2.11 (VISEN)
MI_SENSE3: C14.1, TP3.1, U3.11 (VISEN)
M_SLEEP: U1.12 (NSLEEP_HB), U2.12 (NSLEEP_HB), U3.12 (NSLEEP_HB); also elsewhere on the board
unnamed: R1.1, U1.7 (ISET)
unnamed: C2.1, U1.6 (VCC)
unnamed: R2.1, U2.7 (ISET)
unnamed: C7.1, U2.6 (VCC)
unnamed: R5.1, U3.7 (ISET)
unnamed: C11.1, U3.6 (VCC)
VCC: J1.4, J2.4, J3.4; also elsewhere on the board
Vdrive: C5.1, C6.1, C8.1, C9.1, C12.1, C13.1, U1.9 (VIN), U2.9 (VIN), U3.9 (VIN); also elsewhere on the board

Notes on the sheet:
M_SLEEP: Pull high for H-bridge normal operation. Pull low to disable the H-bridge output and enter low-power sleep mode. Internal pull-down.
Square-marked shape on encoder as the 1st pin. Encoder is facing pins-down. Connector on the encoder is through-holes on a 2mm pitch.
Motor drivers
8.5k-8k is OK
Current limiting: 8.5k Ohm => 0.85V/1A 0.85*0.58~=0.5V
Vdrive = 6V
Encoder connections + Motor power
The MP6550 is fully protected against undervoltage, over-current, and over-temperature events. A continuous current of 1.7 A is sustainable without a thermal shutdown. Max input control frequency: 100 kHz
2k Ohm for ISEN resistor. Current limit occurs when VISEN senses 0.5V. With 2k Ohm it occurs at 2.5A drive current.

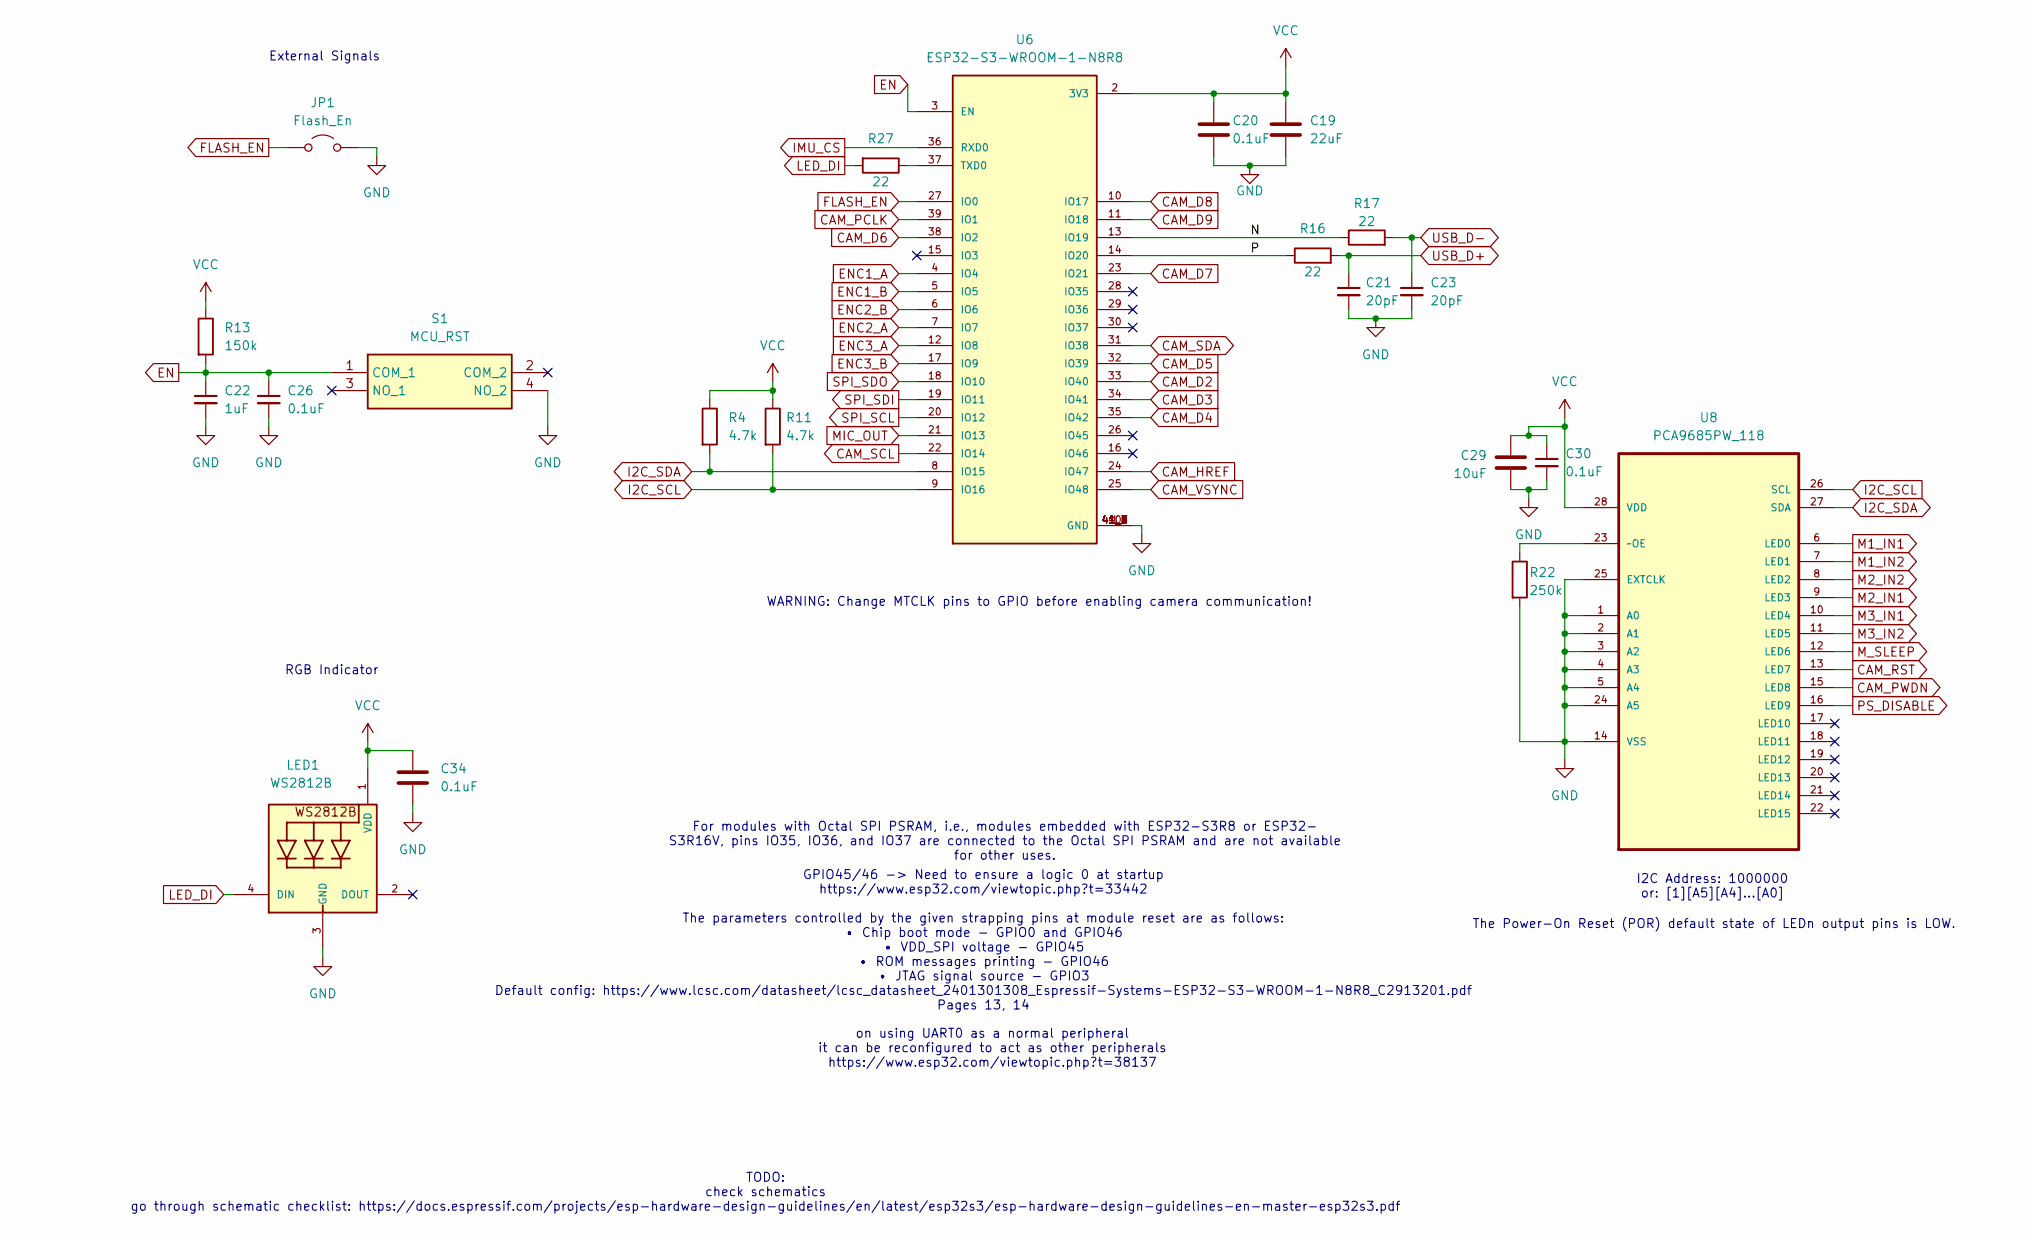
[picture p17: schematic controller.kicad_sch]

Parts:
C19: 22uF; C_0603_1608Metric_Pad1.08x0.95mm_HandSolder
C20, C26, C30, C34: 0.1uF; C_0603_1608Metric_Pad1.08x0.95mm_HandSolder
C21, C23: 20pF; C_0402_1005Metric_Pad0.74x0.62mm_HandSolder
C22: 1uF; CP_EIA-3216-18_Kemet-A_Pad1.58x1.35mm_HandSolder
C29: 10uF; C_1206_3216Metric_Pad1.33x1.80mm_HandSolder
JP1: Flash_En; Flash_Jumper_1x02_P2.00mm_Vertical
LED1: WS2812B
R4, R11: 4.7k; R_0603_1608Metric_Pad0.98x0.95mm_HandSolder
R13: 150k; R_0603_1608Metric_Pad0.98x0.95mm_HandSolder
R16, R17: 22; R_0402_1005Metric_Pad0.72x0.64mm_HandSolder
R22: 250k; R_0603_1608Metric_Pad0.98x0.95mm_HandSolder
R27: 22; R_0603_1608Metric_Pad0.98x0.95mm_HandSolder
S1: MCU_RST; PTS526SK15SMTR2LFS; Manufacturer_Part_Number PTS526 SK15 SMTR2 LFS; Mouser Part Number 611-PTS526SK15SMR2L
U6: ESP32-S3-WROOM-1-N8R8; XCVR_ESP32S3WROOM1N8R8
U8: PCA9685PW_118; SOP65P640X110-28N; MPN PCA9685PW,118

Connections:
/MCU/N: R17.1, U6.13 (IO19)
/MCU/P: R16.1, U6.14 (IO20)
CAM_D2: U6.33 (IO40); also elsewhere on the board
CAM_D3: U6.34 (IO41); also elsewhere on the board
CAM_D4: U6.35 (IO42); also elsewhere on the board
CAM_D5: U6.32 (IO39); also elsewhere on the board
CAM_D6: U6.38 (IO2); also elsewhere on the board
CAM_D7: U6.23 (IO21); also elsewhere on the board
CAM_D8: U6.10 (IO17); also elsewhere on the board
CAM_D9: U6.11 (IO18); also elsewhere on the board
CAM_HREF: U6.24 (IO47); also elsewhere on the board
CAM_PCLK: U6.39 (IO1); also elsewhere on the board
CAM_PWDN: U8.15 (LED8); also elsewhere on the board
CAM_RST: U8.13 (LED7); also elsewhere on the board
CAM_SCL: U6.22 (IO14); also elsewhere on the board
CAM_SDA: U6.31 (IO38); also elsewhere on the board
CAM_VSYNC: U6.25 (IO48); also elsewhere on the board
EN: C22.1, C26.1, R13.2, S1.1 (COM_1), U6.3 (EN)
ENC1_A: U6.4 (IO4); also elsewhere on the board
ENC1_B: U6.5 (IO5); also elsewhere on the board
ENC2_A: U6.7 (IO7); also elsewhere on the board
ENC2_B: U6.6 (IO6); also elsewhere on the board
ENC3_A: U6.12 (IO8); also elsewhere on the board
ENC3_B: U6.17 (IO9); also elsewhere on the board
FLASH_EN: JP1.1 (A), U6.27 (IO0)
GND: C19.2, C20.2, C21.2, C22.2, C23.2, C26.2, C29.1, C30.2, C34.2, JP1.2 (B), LED1.3 (GND), R22.2, S1.4 (NO_2), U6.1 (GND), U6.40 (GND), U6.41_1 (GND), U6.41_2 (GND), U6.41_3 (GND), U6.41_4 (GND), U6.41_5 (GND), U6.41_6 (GND), U6.41_7 (GND), U6.41_8 (GND), U6.41_9 (GND), U8.1 (A0), U8.2 (A1), U8.3 (A2), U8.4 (A3), U8.5 (A4), U8.14 (VSS), U8.24 (A5), U8.25 (EXTCLK); also elsewhere on the board
I2C_SCL: R11.2, U6.9 (IO16), U8.26 (SCL); also elsewhere on the board
I2C_SDA: R4.2, U6.8 (IO15), U8.27 (SDA); also elsewhere on the board
IMU_CS: U6.36 (RXD0); also elsewhere on the board
LED_DI: LED1.4 (DIN), R27.2
M1_IN1: U8.6 (LED0); also elsewhere on the board
M1_IN2: U8.7 (LED1); also elsewhere on the board
M2_IN1: U8.9 (LED3); also elsewhere on the board
M2_IN2: U8.8 (LED2); also elsewhere on the board
M3_IN1: U8.10 (LED4); also elsewhere on the board
M3_IN2: U8.11 (LED5); also elsewhere on the board
MIC_OUT: U6.21 (IO13); also elsewhere on the board
M_SLEEP: U8.12 (LED6); also elsewhere on the board
unnamed: R27.1, U6.37 (TXD0)
unnamed: R22.1, U8.23 (~OE)
PS_DISABLE: U8.16 (LED9); also elsewhere on the board
SPI_SCL: U6.20 (IO12); also elsewhere on the board
SPI_SDI: U6.19 (IO11); also elsewhere on the board
SPI_SDO: U6.18 (IO10); also elsewhere on the board
USB_D+: C21.1, R16.2; also elsewhere on the board
USB_D-: C23.1, R17.2; also elsewhere on the board
VCC: C19.1, C20.1, C29.2, C30.1, C34.1, LED1.1 (VDD), R4.1, R11.1, R13.1, U6.2 (3V3), U8.28 (VDD); also elsewhere on the board

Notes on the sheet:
GPIO45/46 -> Need to ensure a logic 0 at startup https://www.esp32.com/viewtopic.php?t=33442 The parameters controlled by the given strapping pins at module reset are as follows: • Chip boot mode - GPIO0 and GPIO46 • VDD_SPI voltage - GPIO45 • ROM messages printing - GPIO46 • JTAG signal source - G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
TODO: check schematics go through schematic checklist: https://docs.espressif.com/projects/esp-hardware-design-guidelines/en/latest/esp32s3/esp-hardware-design-guidelines-en-master-esp32s3.pdf
External Signals
I2C Address: 1000000 or: [1][A5][A4]...[A0]
on using UART0 as a normal peripheral it can be reconfigured to act as other peripherals https://www.esp32.com/viewtopic.php?t=38137
The Power-On Reset (POR) default state of LEDn output pins is LOW.
RGB Indicator
For modules with Octal SPI PSRAM, i.e., modules embedded with ESP32-S3R8 or ESP32- S3R16V, pins IO35, IO36, and IO37 are connected to the Octal SPI PSRAM and are not available for other uses.
WARNING: Change MTCLK pins to GPIO before enabling camera communication!

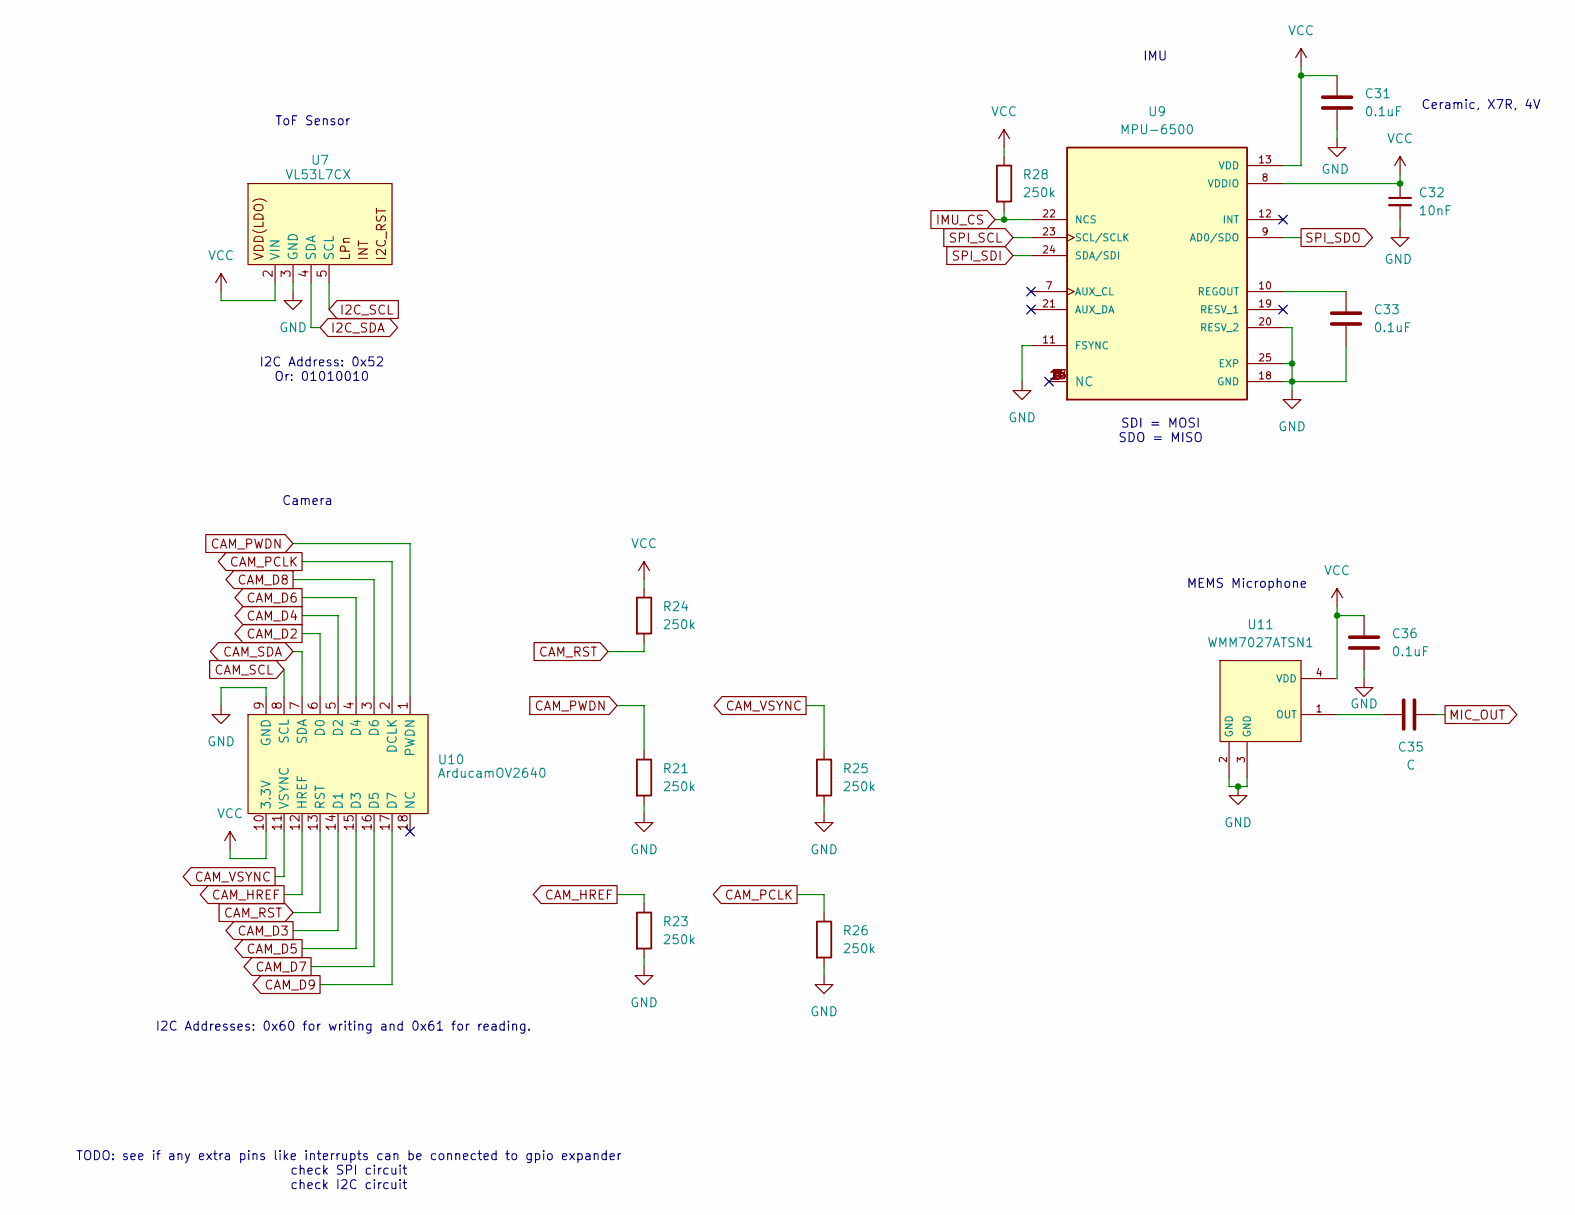
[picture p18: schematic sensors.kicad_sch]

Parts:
C31, C33, C36: 0.1uF; C_0603_1608Metric_Pad1.08x0.95mm_HandSolder
C32: 10nF; C_0603_1608Metric_Pad1.08x0.95mm_HandSolder
C35: C; C_0603_1608Metric_Pad1.08x0.95mm_HandSolder
R21, R23, R24, R25, R26, R28: 250k; R_0603_1608Metric_Pad0.98x0.95mm_HandSolder
U7: VL53L7CX; CONN_S4B-XH-SM4-TB_JST
U9: MPU-6500; QFN24_3X3X0P9_MPU6500; PARTREV 1.3
U10: ArducamOV2640; Arducam_Socket_2x09_P2.54mm_Vertical_SMD
U11: WMM7027ATSN1; WMM7027ATSN1-4TR

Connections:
CAM_D2: U10.6 (D0); also elsewhere on the board
CAM_D3: U10.14 (D1); also elsewhere on the board
CAM_D4: U10.5 (D2); also elsewhere on the board
CAM_D5: U10.15 (D3); also elsewhere on the board
CAM_D6: U10.4 (D4); also elsewhere on the board
CAM_D7: U10.16 (D5); also elsewhere on the board
CAM_D8: U10.3 (D6); also elsewhere on the board
CAM_D9: U10.17 (D7); also elsewhere on the board
CAM_HREF: R23.1, U10.12 (HREF); also elsewhere on the board
CAM_PCLK: R26.1, U10.2 (DCLK); also elsewhere on the board
CAM_PWDN: R21.1, U10.1 (PWDN); also elsewhere on the board
CAM_RST: R24.2, U10.13 (RST); also elsewhere on the board
CAM_SCL: U10.8 (SCL); also elsewhere on the board
CAM_SDA: U10.7 (SDA); also elsewhere on the board
CAM_VSYNC: R25.1, U10.11 (VSYNC); also elsewhere on the board
GND: C31.2, C32.2, C33.2, C36.2, R21.2, R23.2, R25.2, R26.2, U7.3 (GND), U9.11 (FSYNC), U9.18 (GND), U9.20 (RESV_2), U9.25 (EXP), U10.9 (GND), U11.2 (GND), U11.3 (GND); also elsewhere on the board
I2C_SCL: U7.5 (SCL); also elsewhere on the board
I2C_SDA: U7.4 (SDA); also elsewhere on the board
IMU_CS: R28.2, U9.22 (NCS); also elsewhere on the board
MIC_OUT: C35.2; also elsewhere on the board
unnamed: C33.1, U9.10 (REGOUT)
unnamed: C35.1, U11.1 (OUT)
SPI_SCL: U9.23 (SCL/SCLK); also elsewhere on the board
SPI_SDI: U9.24 (SDA/SDI); also elsewhere on the board
SPI_SDO: U9.9 (AD0/SDO); also elsewhere on the board
VCC: C31.1, C32.1, C36.1, R24.1, R28.1, U7.2 (VIN), U9.8 (VDDIO), U9.13 (VDD), U10.10 (3.3V), U11.4 (VDD); also elsewhere on the board

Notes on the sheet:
SDI = MOSI SDO = MISO
Camera
I2C Addresses: 0x60 for writing and 0x61 for reading.
TODO: see if any extra pins like interrupts can be connected to gpio expander check SPI circuit check I2C circuit
Ceramic, X7R, 4V
ToF Sensor
I2C Address: 0x52 Or: 01010010
IMU
MEMS Microphone

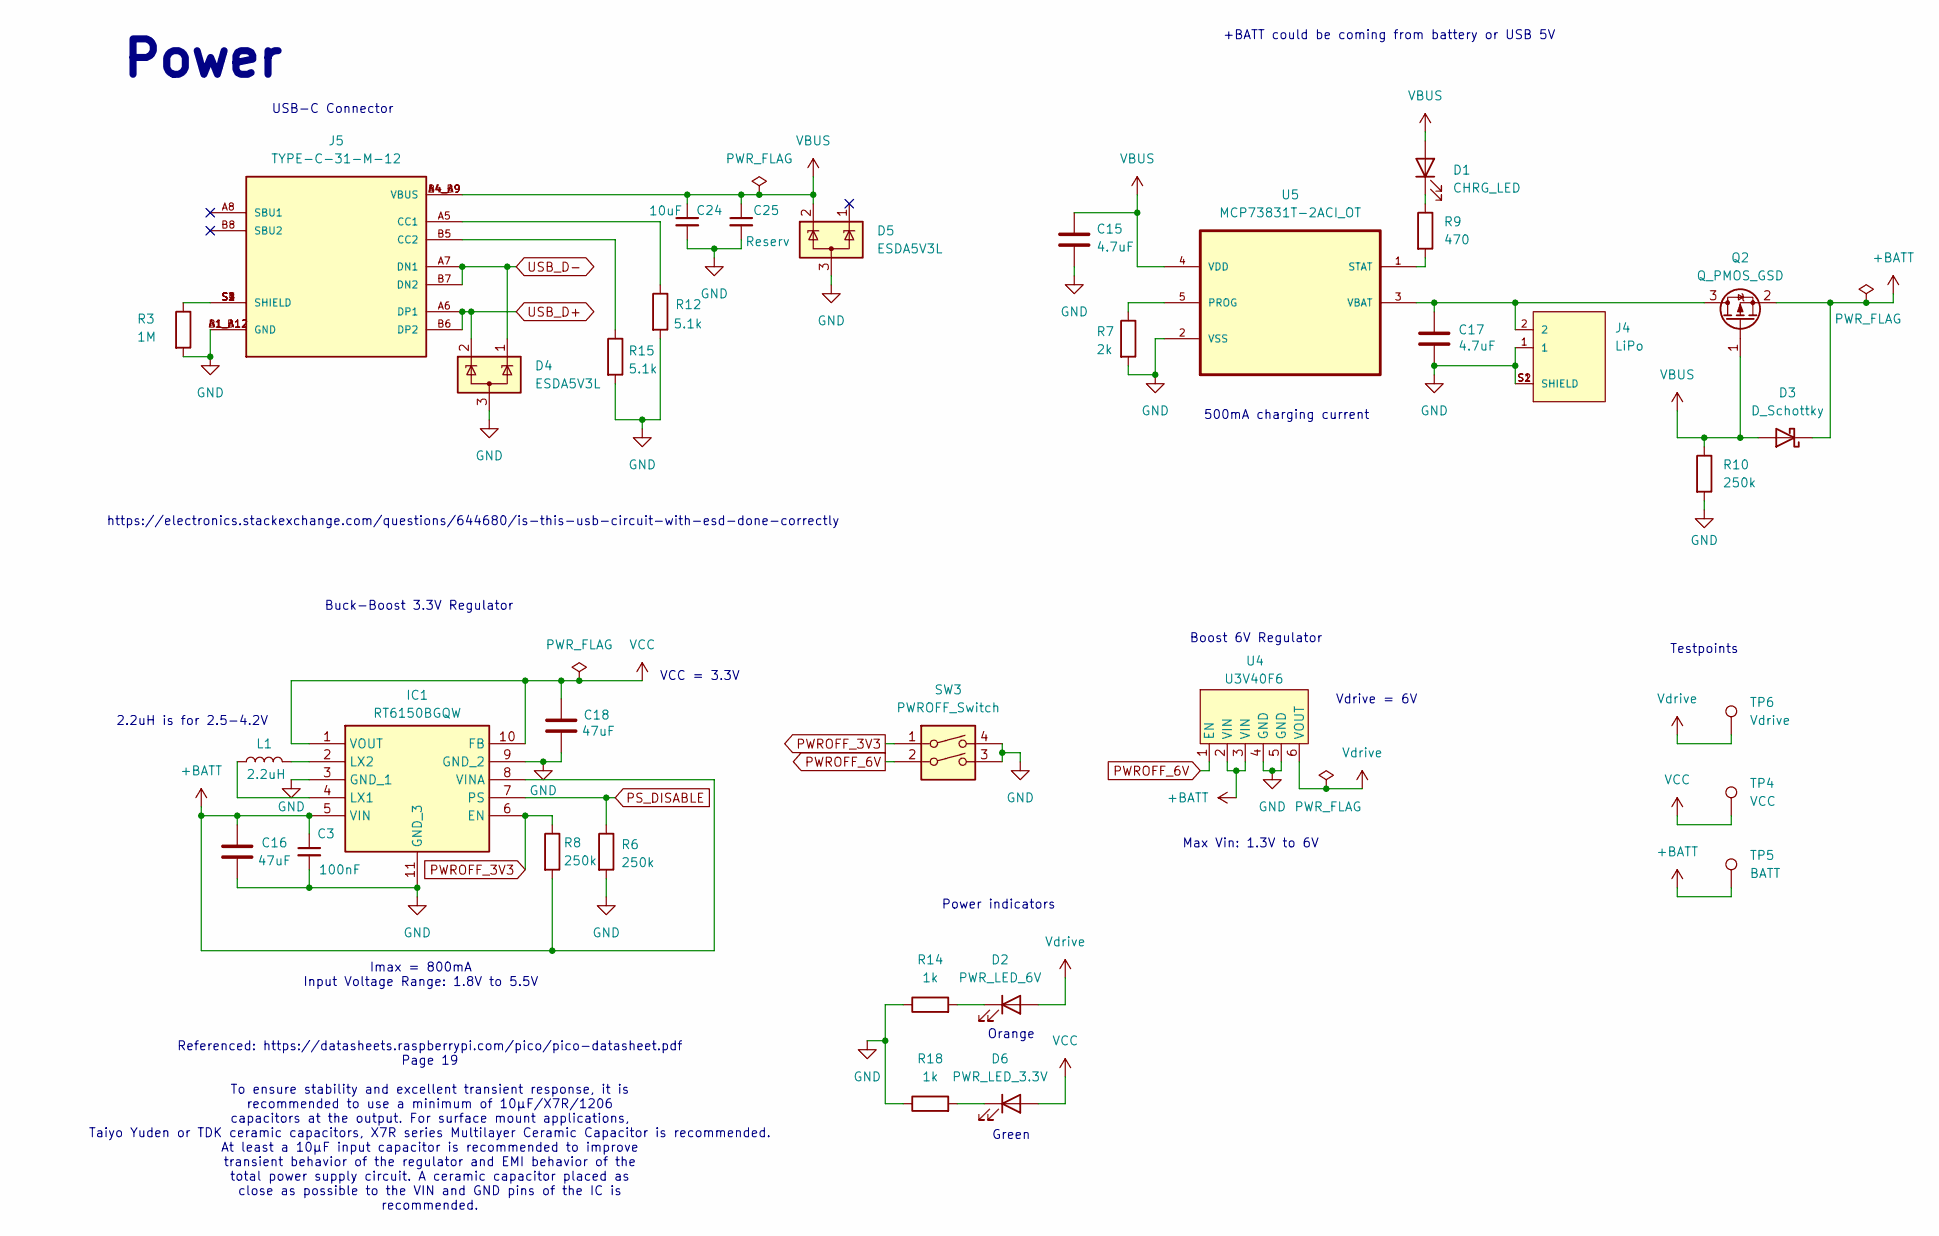
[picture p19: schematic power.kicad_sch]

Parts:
C3: 100nF; C_0603_1608Metric_Pad1.08x0.95mm_HandSolder
C15, C17: 4.7uF; C_0603_1608Metric_Pad1.08x0.95mm_HandSolder
C16, C18: 47uF; C_1210_3225Metric_Pad1.33x2.70mm_HandSolder
C24: 10uF; C_1206_3216Metric_Pad1.33x1.80mm_HandSolder
C25: Reserv; C_0603_1608Metric_Pad1.08x0.95mm_HandSolder
D1: CHRG_LED; LED_0603_1608Metric_Pad1.05x0.95mm_HandSolder
D2: PWR_LED_6V; LED_0805_2012Metric_Pad1.15x1.40mm_HandSolder
D3: D_Schottky; D_SOD-123F
D4, D5: ESDA5V3L; SOT-23
D6: PWR_LED_3.3V; LED_0805_2012Metric_Pad1.15x1.40mm_HandSolder
IC1: RT6150BGQW; SON50P250X250X80-11N-D; Mouser Part Number 835-RT6150BGQW
J4: LiPo; JST_S2B-PH-SM4-TB_LF__SN_
J5: TYPE-C-31-M-12; HRO_TYPE-C-31-M-12; PARTREV 2020.12.08
L1: 2.2uH; FNR4020S2R2MT
Q2: Q_PMOS_GSD; SOT-23
R3: 1M; R_0603_1608Metric_Pad0.98x0.95mm_HandSolder
R6, R8, R10: 250k; R_0603_1608Metric_Pad0.98x0.95mm_HandSolder
R7: 2k; R_0603_1608Metric_Pad0.98x0.95mm_HandSolder
R9: 470; R_0603_1608Metric_Pad0.98x0.95mm_HandSolder
R12, R15: 5.1k; R_0603_1608Metric_Pad0.98x0.95mm_HandSolder
R14, R18: 1k; R_0603_1608Metric_Pad0.98x0.95mm_HandSolder
SW3: PWROFF_Switch; DV7SA-02F-01_SW_DIP_SPSTx02_Slide
TP4: VCC; TestPoint_Pad_1.5x1.5mm
TP5: BATT; TestPoint_Pad_1.5x1.5mm
TP6: Vdrive; TestPoint_Pad_1.5x1.5mm
U4: U3V40F6; U3V40F6_upd
U5: MCP73831T-2ACI_OT; SOT95P280X145-5N; MPN MCP73831T-2ACI/OT

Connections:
+BATT: C3.1, C16.1, D3.1 (K), IC1.5 (VIN), IC1.8 (VINA), Q2.2 (S), R8.2, TP5.1, U4.2 (VIN), U4.3 (VIN)
GND: C3.2, C15.2, C16.2, C17.2, C18.2, C24.2, C25.2, D4.3 (A), D5.3 (A), IC1.3 (GND_1), IC1.9 (GND_2), IC1.11 (GND_3), J4.1, J4.S1 (SHIELD), J4.S2 (SHIELD), J5.A1_B12 (GND), J5.B1_A12 (GND), R3.2, R6.2, R7.2, R10.2, R12.2, R14.1, R15.2, R18.1, SW3.3, SW3.4, U4.4 (GND), U4.5 (GND), U5.2 (VSS); also elsewhere on the board
unnamed: D1.1 (K), R9.1
unnamed: D2.1 (K), R14.2
unnamed: D6.1 (K), R18.2
unnamed: IC1.4 (LX1), L1.1
unnamed: IC1.2 (LX2), L1.2
unnamed: J5.A5 (CC1), R12.1
unnamed: J5.B5 (CC2), R15.1
unnamed: J5.S1 (SHIELD), J5.S2 (SHIELD), J5.S3 (SHIELD), J5.S4 (SHIELD), R3.1
unnamed: C17.1, J4.2, Q2.3 (D), U5.3 (VBAT)
unnamed: R7.1, U5.5 (PROG)
unnamed: R9.2, U5.1 (STAT)
PS_DISABLE: IC1.7 (PS), R6.1; also elsewhere on the board
PWROFF_3V3: IC1.6 (EN), R8.1, SW3.1
PWROFF_6V: SW3.2, U4.1 (EN)
USB_D+: D4.2 (K), J5.A6 (DP1), J5.B6 (DP2); also elsewhere on the board
USB_D-: D4.1 (K), J5.A7 (DN1), J5.B7 (DN2); also elsewhere on the board
VBUS: C15.1, C24.1, C25.1, D1.2 (A), D3.2 (A), D5.2 (K), J5.A4_B9 (VBUS), J5.B4_A9 (VBUS), Q2.1 (G), R10.1, U5.4 (VDD)
VCC: C18.1, D6.2 (A), IC1.1 (VOUT), IC1.10 (FB), TP4.1; also elsewhere on the board
Vdrive: D2.2 (A), TP6.1, U4.6 (VOUT); also elsewhere on the board

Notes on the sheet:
Referenced: https://datasheets.raspberrypi.com/pico/pico-datasheet.pdf Page 19 To ensure stability and excellent transient response, it is recommended to use a minimum of 10μF/X7R/1206 capacitors at the output. For surface mount applications, Taiyo Yuden or TDK ceramic capacitors, X7R series Multil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
Boost 6V Regulator
Testpoints
Vdrive = 6V
Green
Max Vin: 1.3V to 6V
2.2uH is for 2.5-4.2V
500mA charging current
Buck-Boost 3.3V Regulator
Power indicators
Power
https://electronics.stackexchange.com/questions/644680/is-this-usb-circuit-with-esd-done-correctly
+BATT could be coming from battery or USB 5V
VCC = 3.3V
USB-C Connector
Orange
Imax = 800mA Input Voltage Range: 1.8V to 5.5V

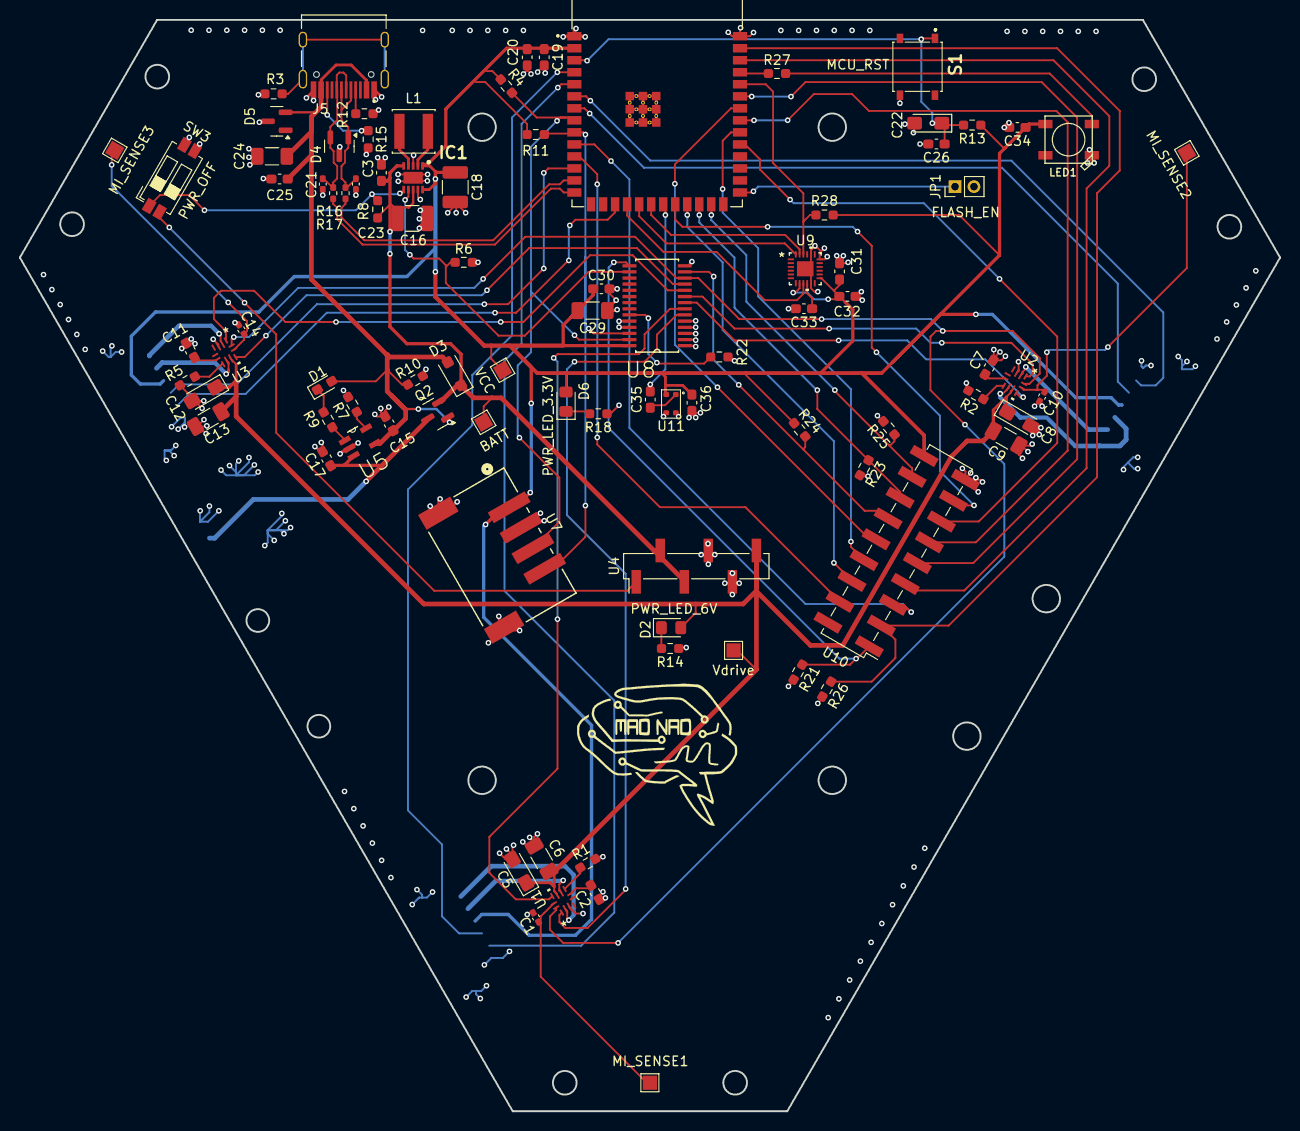
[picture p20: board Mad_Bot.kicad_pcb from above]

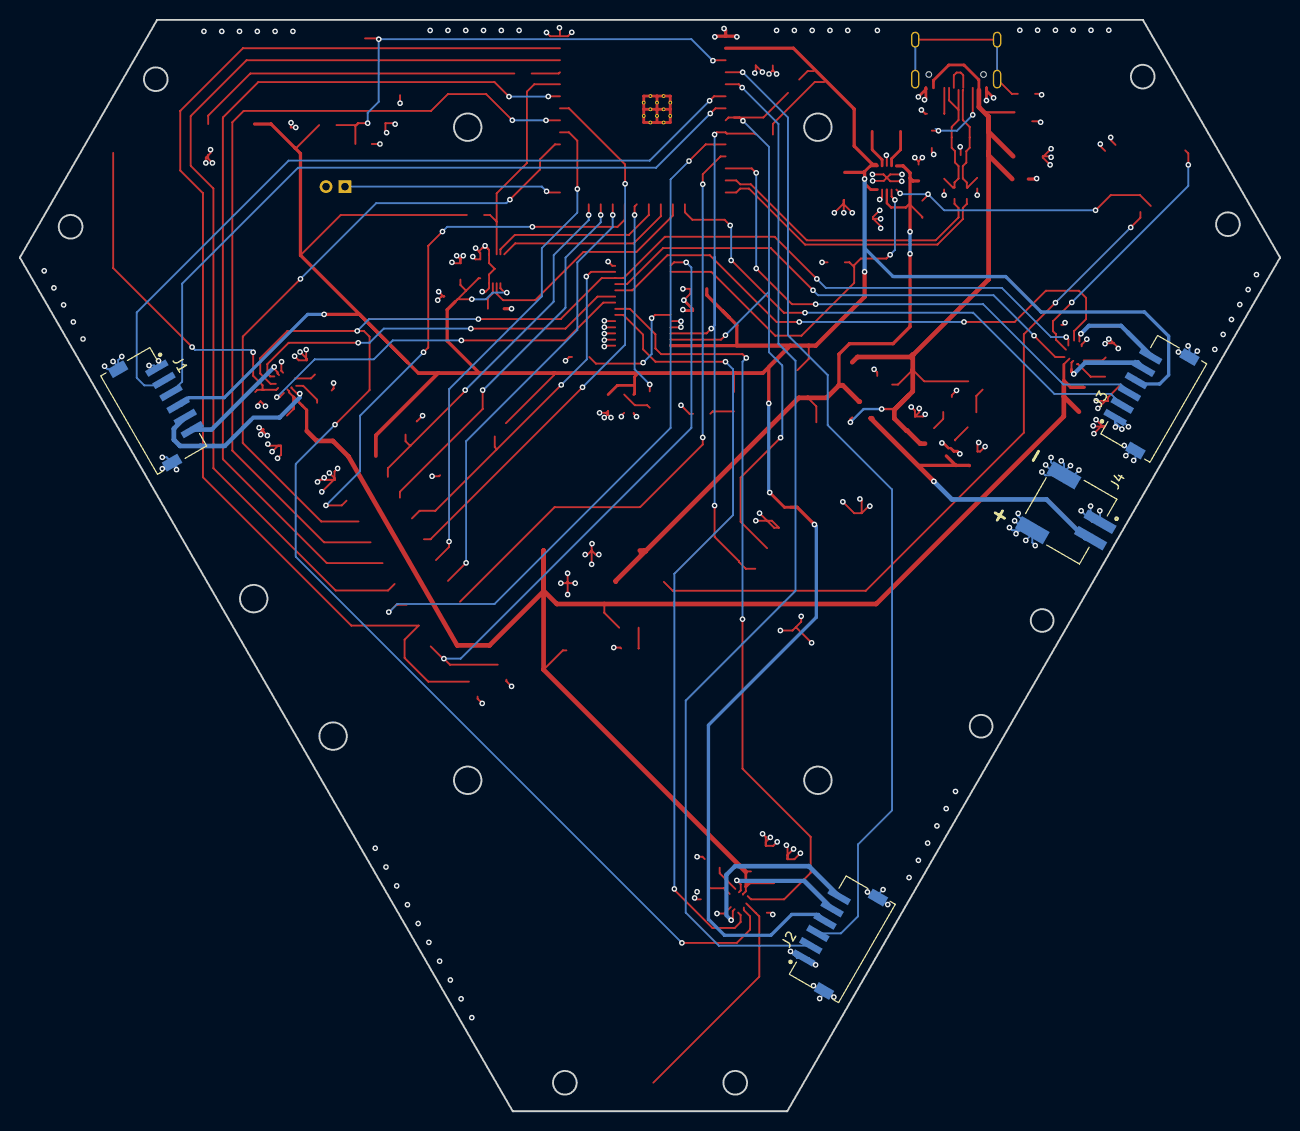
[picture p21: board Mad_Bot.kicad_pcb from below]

Board: 4 copper layers, 133.1 x 115.3 mm, 94 parts (4 on the bottom side), 80 nets.

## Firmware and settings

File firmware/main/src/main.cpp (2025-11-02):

#include <stdio.h>
// #include <stdlib.h>
#include <string.h>
#include <unistd.h>

#include <esp_system.h>
#include <esp_log.h>
#include <nvs_flash.h>
#include <esp_event.h>
#include <esp_netif.h>
#include <esp_err.h>
#include <freertos/FreeRTOS.h>
#include <freertos/task.h>
// #include <freertos/event_groups.h>

// #include <protocol_examples_common.h>

#include <uros_network_interfaces.h>
#include <rcl/rcl.h>
#include <rcl/error_handling.h>
#include <std_msgs/msg/int32.h>
#include <std_msgs/msg/float64_multi_array.h>
#include <sensor_msgs/msg/imu.h>
#include <std_msgs/msg/bool.h>
#include <rclc/rclc.h>
#include <rclc/executor.h>
#include <micro_ros_utilities/type_utilities.h>
#include <micro_ros_utilities/string_utilities.h>

#include "MPU.hpp"        // main file, provides the class itself
#include "mpu/math.hpp"   // math helper for dealing with MPU data
#include "mpu/types.hpp"  // MPU data types and definitions

#include "hardware.h"
#include "demo.h"
#include "motors.h"

static const char *TAG = "MadBot";

#ifdef CONFIG_MICRO_ROS_ESP_XRCE_DDS_MIDDLEWARE
#include <rmw_microros/rmw_microros.h>
#endif

#define RCCHECK(fn) { rcl_ret_t temp_rc = fn; if((temp_rc != RCL_RET_OK)){printf("Failed status on line %d: %d. Aborting.\n",__LINE__,(int)temp_rc);vTaskDelete(NULL);}}
#define RCSOFTCHECK(fn) { rcl_ret_t temp_rc = fn; if((temp_rc != RCL_RET_OK)){printf("Failed status on line %d: %d. Continuing.\n",__LINE__,(int)temp_rc);}}

rcl_publisher_t publisher;
rcl_subscription_t wheels_rpm_subscriber;
rcl_subscription_t motion_cmd_subscriber;
std_msgs__msg__Float64MultiArray wheel_w_msg;
std_msgs__msg__Bool cmd_msg;
sensor_msgs__msg__Imu msg;

extern MPU_t MPU;
mpud::float_axes_t accelG;   // accel axes in (g) gravity format
mpud::float_axes_t gyroDPS;    // gyro axes in (dps) degrees per second format
extern MotorController motors;
volatile bool motion_enabled = false;

double wheel_w_buffer[NUM_WHEELS] = {0};

void IMU_task(void* arg)
{
    mpud::raw_axes_t accelRaw;   // x, y, z axes as int16
	mpud::raw_axes_t gyroRaw;    // x, y, z axes as int16
	int16_t temp = 0;
	float tempC = 0.0f;

    while (1) {
        // Read
        MPU.motion(&accelRaw, &gyroRaw);  // read both in one shot
		temp = MPU.temperature(&temp);
        // Convert
        accelG = mpud::accelGravity(accelRaw, mpud::ACCEL_FS_4G);
		gyroDPS = mpud::gyroDegPerSec(gyroRaw, mpud::GYRO_FS_500DPS);
		tempC = mpud::tempCelsius(temp);
        // Debug
		// printf("WHO_AM_I = 0x%02X\n", MPU.whoAmI());
        // printf("accel: [%+6.2f %+6.2f %+6.2f ] (G) \t gyro: [%+7.2f %+7.2f %+7.2f ] (DPS) \t temp: %+6.2f (C)\n", accelG.x, accelG.y, accelG.z, gyroDPS[0], gyroDPS[1], gyroDPS[2], tempC);
        vTaskDelay(50 / portTICK_PERIOD_MS);
    }
}

void motion_command_callback(const void * msgin)
{
	const std_msgs__msg__Bool* cmd = (const std_msgs__msg__Bool *)msgin;

	if (motion_enabled == cmd->data) // No change
        return;

    if (!cmd->data) {
        ESP_ERROR_CHECK(motors.brake());
    }
    motion_enabled = cmd->data;
}

void wheels_rpm_callback(const void * msgin)
{
	const std_msgs__msg__Float64MultiArray* cmd = (const std_msgs__msg__Float64MultiArray *)msgin;

    if (!motion_enabled) {// No change 
    	return;
	}

	for (size_t i = 0; i < NUM_WHEELS; i++) {
		printf("Wheel %d cmd: %f rad/s\n", (int)i, wheel_w_buffer[i]);
		// wheel_w_buffer[i] = cmd->data.data[i];
	}
	ESP_ERROR_CHECK(motors.setWheelVelocities(wheel_w_buffer));
}

void timer_callback(rcl_timer_t * timer, int64_t last_call_time)
{
	RCLC_UNUSED(last_call_time);
	if (timer != NULL) {
        msg.linear_acceleration.x = accelG.x;
        msg.linear_acceleration.y = accelG.y;
        msg.linear_acceleration.z = accelG.z;
		msg.angular_velocity.x = gyroDPS.x;
		msg.angular_velocity.y = gyroDPS.y;
		msg.angular_velocity.z = gyroDPS.z;

		// printf("Publishing: %d\n", (int) msg_test.data);
		RCSOFTCHECK(rcl_publish(&publisher, &msg, NULL));
	}
}

void micro_ros_task(void * arg)
{
	rcl_allocator_t allocator = rcl_get_default_allocator();
	rclc_support_t support;

	rcl_init_options_t init_options = rcl_get_zero_initialized_init_options();
	RCCHECK(rcl_init_options_init(&init_options, allocator));

#ifdef CONFIG_MICRO_ROS_ESP_XRCE_DDS_MIDDLEWARE
	rmw_init_options_t* rmw_options = rcl_init_options_get_rmw_init_options(&init_options);

	// Static Agent IP and port can be used instead of autodisvery.
	RCCHECK(rmw_uros_options_set_udp_address(CONFIG_MICRO_ROS_AGENT_IP, CONFIG_MICRO_ROS_AGENT_PORT, rmw_options));
	//RCCHECK(rmw_uros_discover_agent(rmw_options));
#endif

	// create init_options
	RCCHECK(rclc_support_init_with_options(&support, 0, NULL, &init_options, &allocator));

	// create node
	rcl_node_t node;
	RCCHECK(rclc_node_init_default(&node, "esp32_publisher", "", &support));
	
	// create publisher
	// RCCHECK(rclc_publisher_init_best_effort(
	// 	&publisher_test,
	// 	&node,
	// 	ROSIDL_GET_MSG_TYPE_SUPPORT(std_msgs, msg, Int32),
	// 	"/microROS/int32_publisher"));

    // create publisher
	RCCHECK(rclc_publisher_init_default(
		&publisher,
		&node,
    	ROSIDL_GET_MSG_TYPE_SUPPORT(sensor_msgs, msg, Imu),
		"/microROS/IMU_publisher"));

	 // Create subscribers.
	RCCHECK(rclc_subscription_init_default(
		&wheels_rpm_subscriber,
		&node,
		ROSIDL_GET_MSG_TYPE_SUPPORT(std_msgs, msg, Float64MultiArray),
		"/wheels_controller/commands"));
	RCCHECK(rclc_subscription_init_default(
		&motion_cmd_subscriber,
		&node,
		ROSIDL_GET_MSG_TYPE_SUPPORT(std_msgs, msg, Bool),
		"/motion_command"));


	// create timer,
	rcl_timer_t timer;
	const unsigned int timer_timeout = 2000;
	RCCHECK(rclc_timer_init_default(
		&timer,
		&support,
		RCL_MS_TO_NS(timer_timeout),
		timer_callback));

	// create executor
	rclc_executor_t executor;
	RCCHECK(rclc_executor_init(&executor, &support.context, 3, &allocator));
	RCCHECK(rclc_executor_add_timer(&executor, &timer));
	RCCHECK(rclc_executor_add_subscription(&executor, &wheels_rpm_subscriber, &wheel_w_msg, &wheels_rpm_callback, ON_NEW_DATA));
	RCCHECK(rclc_executor_add_subscription(&executor, &motion_cmd_subscriber, &cmd_msg, &motion_command_callback, ON_NEW_DATA));

    static micro_ros_utilities_memory_conf_t conf = {0};
    conf.max_string_capacity = 50;
	conf.max_ros2_type_sequence_capacity = 5;
	conf.max_basic_type_sequence_capacity = 5;

	// OPTIONALLY this struct can store rules for specific members
	// !! Using the API with rules will use dynamic memory allocations for handling strings !!

	micro_ros_utilities_memory_rule_t rules[] = {
		{"header.frame_id", 30},
	};
	conf.rules = rules;
	conf.n_rules = sizeof(rules) / sizeof(rules[0]);
    size_t dynamic_size = micro_ros_utilities_get_dynamic_size(
		ROSIDL_GET_MSG_TYPE_SUPPORT(sensor_msgs, msg, Imu),
		conf
	);
	// The total (stack, static & dynamic) memory usage of a packet will be:
	size_t message_total_size = dynamic_size + sizeof(sensor_msgs__msg__Imu);
    // The message dynamic memory can be allocated using the following call.
	// This will use rcutils default allocators for getting memory.
	bool success = micro_ros_utilities_create_message_memory(
		ROSIDL_GET_MSG_TYPE_SUPPORT(sensor_msgs, msg, Imu),
		&msg,
		conf
	);
    msg.header.frame_id = micro_ros_string_utilities_set(msg.header.frame_id, "madbot");

	msg.orientation.x = 0.0;
    msg.orientation.y = 0.0;
    msg.orientation.z = 0.0;
    msg.orientation.w = 1.0;
    msg.angular_velocity.x = 0.0;
    msg.angular_velocity.y = 0.0;
    msg.angular_velocity.z = 0.0;
    msg.linear_acceleration.x = 0.0;
    msg.linear_acceleration.y = 0.0;
    msg.linear_acceleration.z = 0.0;

	wheel_w_msg.data.size = NUM_WHEELS;
	wheel_w_msg.data.capacity = NUM_WHEELS;
	wheel_w_msg.data.data = wheel_w_buffer;

	while (1) {
		rclc_executor_spin_some(&executor, RCL_MS_TO_NS(100));
		usleep(100);
	}

	// free resources
	RCCHECK(rcl_publisher_fini(&publisher, &node));
	RCCHECK(rcl_subscription_fini(&wheels_rpm_subscriber, &node));
	RCCHECK(rcl_subscription_fini(&motion_cmd_subscriber, &node));
	RCCHECK(rcl_node_fini(&node));

  	vTaskDelete(NULL);
}

// void synch_time_with_agent()
// {
//     // Sync timeout
//     const int timeout_ms = 5000;

//     // Synchronize time with the agent
//     RCCHECK(rmw_uros_sync_session(timeout_ms));

//     if (rmw_uros_epoch_synchronized())
//     {
//         // Get time in milliseconds or nanoseconds
//         //base_timestamp_ms = rmw_uros_epoch_millis();
//         base_timestamp_ns = rmw_uros_epoch_nanos();
//         base_timestamp_s = base_timestamp_ns / 1000000000;
//         base_timestamp_ns = base_timestamp_ns % 1000000000; // convert into fractional part
//     }
//     baseline_ticks = xTaskGetTickCount();
//     printf("Baseline ticks: %lld\n", baseline_ticks);
//     printf("Base timestamp (s): %lld\n", base_timestamp_s);
//     printf("Base timestamp (fraction) (ns): %lld\n", base_timestamp_ns);
// }


extern "C" void app_main() {
    // hardware initialization

	// ESP_ERROR_CHECK(nvs_flash_init());
    // ESP_ERROR_CHECK(esp_netif_init());
    // ESP_ERROR_CHECK(esp_event_loop_create_default());

	// ESP_ERROR_CHECK(example_connect()); //old Wi-Fi connection

    #if defined(CONFIG_MICRO_ROS_ESP_NETIF_WLAN) || defined(CONFIG_MICRO_ROS_ESP_NETIF_ENET)
        ESP_ERROR_CHECK(uros_network_interface_initialize());
    #endif

    hardware_init();

	// task_Demo(Command::FORWARD);
	// vTaskDelay(1000 / portTICK_PERIOD_MS);
	// task_Demo(Command::BACKWARD);
	// vTaskDelay(1000 / portTICK_PERIOD_MS);
	// task_Demo(Command::ROTATE);
	// vTaskDelay(1000 / portTICK_PERIOD_MS);

    // pin micro-ros task in APP_CPU to make PRO_CPU to deal with wifi:
    xTaskCreate(IMU_task,
            "IMU_task",
            CONFIG_MICRO_ROS_APP_STACK,
            NULL,
            CONFIG_MICRO_ROS_APP_TASK_PRIO,
            NULL);
    
    xTaskCreate(micro_ros_task,
            "uros_task",
            CONFIG_MICRO_ROS_APP_STACK,
            NULL,
            CONFIG_MICRO_ROS_APP_TASK_PRIO,
            NULL);

    esp_log_level_set("wifi", ESP_LOG_NONE);
	// ESP_ERROR_CHECK(start_http_demo_server());

	// synch_time_with_agent();
}

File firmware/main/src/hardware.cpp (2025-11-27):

#include "sdkconfig.h"

#include <math.h>

#include <esp_log.h>
#include <freertos/FreeRTOS.h>
#include <freertos/task.h>

#include <driver/i2c.h>
#include <driver/pulse_cnt.h>
#include <driver/gpio.h>

#include "pca9685.h"
#include "MPU.hpp"        // main file, provides the class itself
#include "mpu/math.hpp"   // math helper for dealing with MPU data
#include "mpu/types.hpp"  // MPU data types and definitions
#include "SPIbus.hpp"
// #include "vl53l5cx_api.h"
#include "hardware.h"
#include "pinout.h"
#include "motors.h"

#include "vl53l7cx_api.h" 

static char TAG[] = "HARDWARE";

#undef ESP_ERROR_CHECK
#define ESP_ERROR_CHECK(x)   do { esp_err_t rc = (x); if (rc != ESP_OK) { ESP_LOGE("err", "esp_err_t = %d", rc); assert(0 && #x);} } while(0);

// Globals
i2c_port_t i2c_master_port = I2C_MASTER_NUM;
pcnt_unit_handle_t pcnt_unit1 = NULL;
pcnt_unit_handle_t pcnt_unit2 = NULL;
pcnt_unit_handle_t pcnt_unit3 = NULL;
MPU_t MPU;  // create a default MPU object
spi_device_handle_t mpu_spi_handle;

MotorController::MotorConfig mA = {
    .in1 = M1_IN1,
    .in2 = M1_IN2,
};
MotorController::MotorConfig mB = {
    .in1 = M2_IN1,
    .in2 = M2_IN2,
};
MotorController::MotorConfig mC = {
    .in1 = M3_IN1,
    .in2 = M3_IN2,
};
MotorController motors = MotorController(mA, mB, mC);

static void i2c_example_master_init(void);

int vl53l7cx_init_test(void)
{

	/*********************************/
	/*   VL53L7CX ranging variables  */
	/*********************************/

	uint8_t 				status, loop, isAlive, isReady, i;
	VL53L7CX_Configuration 	Dev;			/* Sensor configuration */
	VL53L7CX_ResultsData 	Results;		/* Results data from VL53L7CX */


	/*********************************/
	/*      Customer platform        */
	/*********************************/

	/* Fill the platform structure with customer's implementation. For this
	* example, only the I2C address is used.
	*/
	Dev.platform.address = VL53L7CX_DEFAULT_I2C_ADDRESS;
    Dev.platform.port = I2C_MASTER_NUM;

	/* (Optional) Reset sensor toggling PINs (see platform, not in API) */
	//Reset_Sensor(&(Dev.platform));

	/* (Optional) Set a new I2C address if the wanted address is different
	* from the default one (filled with 0x20 for this example).
	*/
	//status = vl53l7cx_set_i2c_address(&Dev, 0x20);


	/*********************************/
	/*   Power on sensor and init    */
	/*********************************/

	/* (Optional) Check if there is a VL53L7CX sensor connected */
	status = vl53l7cx_is_alive(&Dev, &isAlive);
	if(!isAlive || status)
	{
		printf("VL53L7CX not detected at requested address\n");
		return status;
	}

	/* (Mandatory) Init VL53L7CX sensor */
	status = vl53l7cx_init(&Dev);
	if(status)
	{
		printf("VL53L7CX ULD Loading failed\n");
		return status;
	}

	printf("VL53L7CX ULD ready ! (Version : %s)\n",
			VL53L7CX_API_REVISION);


    status = vl53l7cx_set_resolution(&Dev, VL53L7CX_RESOLUTION_8X8);        

	/*********************************/
	/*         Ranging loop          */
	/*********************************/

	status = vl53l7cx_start_ranging(&Dev);

	loop = 0;
	while(loop < 10)
	{
		/* Use polling function to know when a new measurement is ready.
		 * Another way can be to wait for HW interrupt raised on PIN A3
		 * (GPIO 1) when a new measurement is ready */
 
		status = vl53l7cx_check_data_ready(&Dev, &isReady);

		if(isReady)
		{
			vl53l7cx_get_ranging_data(&Dev, &Results);

			/* As the sensor is set in 4x4 mode by default, we have a total 
			 * of 16 zones to print. For this example, only the data of first zone are 
			 * print */
			printf("Print data no : %3u\n", Dev.streamcount);
			for(i = 0; i < 16; i++)
			{
				printf("Zone : %3d, Status : %3u, Distance : %4d mm\n",
					i,
					Results.target_status[VL53L7CX_NB_TARGET_PER_ZONE*i],
					Results.distance_mm[VL53L7CX_NB_TARGET_PER_ZONE*i]);
			}
			printf("\n");
			loop++;
		}

		/* Wait a few ms to avoid too high polling (function in platform
		 * file, not in API) */
		WaitMs(&(Dev.platform), 5);
	}

	status = vl53l7cx_stop_ranging(&Dev);
	printf("End of ULD demo\n");
	return status;
}

// TODO: one callback for all units?
static bool pcnt_on_reach1(pcnt_unit_handle_t unit, const pcnt_watch_event_data_t *edata, void *user_ctx)
{
    BaseType_t high_task_wakeup;
    QueueHandle_t queue = (QueueHandle_t)user_ctx;
    // send event data to queue, from this interrupt callback
    xQueueSendFromISR(queue, &(edata->watch_point_value), &high_task_wakeup);
    return (high_task_wakeup == pdTRUE);
}

static bool pcnt_on_reach2(pcnt_unit_handle_t unit, const pcnt_watch_event_data_t *edata, void *user_ctx)
{
    BaseType_t high_task_wakeup;
    QueueHandle_t queue = (QueueHandle_t)user_ctx;
    // send event data to queue, from this interrupt callback
    xQueueSendFromISR(queue, &(edata->watch_point_value), &high_task_wakeup);
    return (high_task_wakeup == pdTRUE);
}
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

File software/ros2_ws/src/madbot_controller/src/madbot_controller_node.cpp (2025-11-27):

#include <cstdio>

#include <chrono>
#include <memory>
#include <iostream>
#include <cmath>
#include <vector>
#include <cstdlib>
#include <stdexcept>

#include "rclcpp/rclcpp.hpp"
#include "std_msgs/msg/float64_multi_array.hpp"
#include "geometry_msgs/msg/twist.hpp"
// #include "geometry_msgs/msg/transform_stamped.hpp"
// #include "nav_msgs/msg/odometry.hpp"
// #include "sensor_msgs/msg/joint_state.hpp"
// #include "sensor_msgs/msg/imu.hpp"
// #include <tf2_ros/transform_broadcaster.h>
#include <tf2/LinearMath/Quaternion.h>
#include <tf2/LinearMath/Matrix3x3.h>
#include <Eigen/Dense>

using namespace std::chrono_literals;
using std::placeholders::_1;
using namespace std;

// Wheel diameter: 38 mm
// Robot radius: 96.896 mm
#define WHEEL_COUNT         3
#define WHEEL_RADIUS        0.019
#define ROBOT_RADIUS        0.096896

class MadBotController : public rclcpp::Node
{
public:
  MadBotController(int num_wheels_, double robot_radius_, double wheel_radius_, double heading_offset_ = 0)
  : Node("madbot_controller_node")
  {
    N = num_wheels_; // num of wheel
    R = robot_radius_;
    r = wheel_radius_;
    heading_offset = heading_offset_;

    tM = init_transform_matrix(N, heading_offset_);
    // cout << "tM:" << endl;
    // cout << tM << endl;

    tMI = pseudo_inverse(tM);
    tMI = Eigen::MatrixXd(tMI.block(0, 0, 2, tMI.cols()));
    // cout << "tMI:" << endl;
    // cout << tMI << endl;
    
    for(int i = 1; i < N+1; i++) {
      string joint_name = "omni_wheel_joint_" + to_string(i);
      wheel_joint_map_index[joint_name] = i - 1;
    }

    for(int i = 0; i < N; i++){
      string topic_name = "wheel" + to_string(i+1) + "_controller/commands";
      auto pub = this->create_publisher<std_msgs::msg::Float64MultiArray>(topic_name, 10);
      pub_wheels.push_back(pub);
    }
    pub_all_wheels = this->create_publisher<std_msgs::msg::Float64MultiArray>("wheels_controller/commands", 10);

    // pub_odometry = this->create_publisher<nav_msgs::msg::Odometry>("odom", 10);

    sub_cmd_vel = this->create_subscription<geometry_msgs::msg::Twist>("cmd_vel", 10, std::bind(&MadBotController::cmd_vel_callback, this, _1));
    // sub_join_states = this->create_subscription<sensor_msgs::msg::JointState>("joint_states", 10, std::bind(&MadBotController::join_states_callback, this, _1));
    // sub_imu = this->create_subscription<sensor_msgs::msg::Imu>("imu", 10, std::bind(&MadBotController::imu_callback, this, _1));

    // tf_broadcaster = std::make_shared<tf2_ros::TransformBroadcaster>(*this);

    last_time = this->get_clock()->now();

    double C = 2 * r / sqrt(3);
    double h = 0 * M_PI / 180;
    mOd[0][0] = C * (cos(2 * M_PI / 3 + h) - (cos(2 * M_PI / 3 + h) - cos(h)) / 3);
    mOd[0][1] = C * (-cos(h) - (cos(2 * M_PI / 3 + h) - cos(h)) / 3);
    mOd[0][2] = C * (-(cos(2 * M_PI / 3 + h) - cos(h)) / 3);
    mOd[1][0] = C * (sin(2 * M_PI / 3 + h) - (sin(2 * M_PI / 3 + h) - sin(h)) / 3);
    mOd[1][1] = C * (-sin(h) - (sin(2 * M_PI / 3 + h) - sin(h)) / 3);
    mOd[1][2] = C * (-(sin(2 * M_PI / 3 + h) - sin(h)) / 3);
  }

  ~MadBotController() {
    cout << "MadBotController Destroyed" << endl;
  }

private:
  rclcpp::TimerBase::SharedPtr timer_;
  rclcpp::Publisher<std_msgs::msg::Float64MultiArray>::SharedPtr pub_all_wheels;
  vector<rclcpp::Publisher<std_msgs::msg::Float64MultiArray>::SharedPtr> pub_wheels;
  // rclcpp::Publisher<nav_msgs::msg::Odometry>::SharedPtr pub_odometry;
  rclcpp::Subscription<geometry_msgs::msg::Twist>::SharedPtr sub_cmd_vel;
  // rclcpp::Subscription<sensor_msgs::msg::JointState>::SharedPtr sub_join_states;
  // rclcpp::Subscription<sensor_msgs::msg::Imu>::SharedPtr sub_imu;

  // std::shared_ptr<tf2_ros::TransformBroadcaster> tf_broadcaster;

  Eigen::MatrixXd tM; //transform matrix from command speed to wheel speed 
  Eigen::MatrixXd tMI; //Inverse Matrix of tM which is a transform matrix from wheel speed to command speed 
  unordered_map<string, int> wheel_joint_map_index; // list of wheel joint name with its index

  // size_t count_;
  int N; // num of wheel
  double r; // wheel radius
  double R; // Robot Radius
  double heading_offset;
  double mOd[2][3] = {{0, 0, 0}, {0, 0, 0}};
  double pos_x = 0;
  double pos_y = 0;
  double vx = 0;
  double vy = 0;
  double pitch = 0, roll = 0, yaw = 0;
  double w = 0;

  rclcpp::Time last_time;

  template <typename T>
  void print_vector(vector<T>& vec) {
    std::cout << "[ ";
    for (const auto& elem : vec) {
        std::cout << elem << " ";
    }
    std::cout << "]" << std::endl;
  }

  void cmd_vel_callback(const geometry_msgs::msg::Twist::SharedPtr msg) {
    Eigen::VectorXd M = calculate_motor_speed(msg->linear.x, msg->linear.y, msg->angular.z);
    set_all_motors_speed(M);
  }

  // void join_states_callback(const sensor_msgs::msg::JointState::SharedPtr msg) {
  //       Eigen::VectorXd w(N);

  //       // Loop through all joint names and extract the velocities for the specified joints
  //       for (size_t i = 0; i < msg->name.size(); ++i)
  //       {
  //         for (const auto& pair : wheel_joint_map_index) {
  //           if (msg->name[i] == pair.first){
  //               w(pair.second) = msg->velocity[i];
  //               break;
  //           }
  //         }
  //       }
        
  //       rclcpp::Time current_time = this->get_clock()->now();
  //       double dt = (current_time - last_time).seconds();
  //       last_time = current_time;
        
  //       Eigen::Matrix2d rM;
  //       rM << cos(yaw), -sin(yaw),
  //             sin(yaw), cos(yaw);
  //       Eigen::MatrixXd dp = rM * tMI * w * dt;
        
  //       pos_x += dp(0);
  //       pos_y += dp(1);
  //       // RCLCPP_INFO(this->get_logger(), "%f %f %f %f %f", w1, w2, w3, vx, vy);
  //       publish_odom(current_time);
  // }

  // void imu_callback(const sensor_msgs::msg::Imu::SharedPtr msg) {
  //   w = msg->angular_velocity.z;
  //   // Convert quaternion to yaw (heading)
  //   tf2::Quaternion q(
  //       msg->orientation.x,
  //       msg->orientation.y,
  //       msg->orientation.z,
  //       msg->orientation.w
  //   );

  //   tf2::Matrix3x3 m(q);
  //   m.getRPY(roll, pitch, yaw); // Extract roll, pitch, and yaw

  //   // RCLCPP_INFO(this->get_logger(), "Yaw: %f", yaw);
  // }

  // void publish_odom(rclcpp::Time current_time) {
  //   // Create the odometry message
  //   nav_msgs::msg::Odometry odom_msg;
  //   odom_msg.header.stamp = current_time;
  //   odom_msg.header.frame_id = "odom";
  //   odom_msg.child_frame_id = "base_footprint";

  //   // Position
  //   odom_msg.pose.pose.position.x = pos_x;
  //   odom_msg.pose.pose.position.y = pos_y;
  //   odom_msg.pose.pose.position.z = 0.0;

  //   // Orientation (Quaternion)
  //   tf2::Quaternion q;
  //   q.setRPY(0, 0, yaw);
  //   odom_msg.pose.pose.orientation.x = q.x();
  //   odom_msg.pose.pose.orientation.y = q.y();
  //   odom_msg.pose.pose.orientation.z = q.z();
  //   odom_msg.pose.pose.orientation.w = q.w();
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

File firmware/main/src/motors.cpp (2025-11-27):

#include "motors.h"
#include "sdkconfig.h"

#include <math.h>

#include <esp_log.h>
#include <freertos/FreeRTOS.h>
#include <freertos/task.h>

#include "pca9685.h"

#include "hardware.h"
#include "pinout.h"

// TODO: check float to int16 conversion
// check how on/off values are set (I suspect that going lower increases speed?)
// check each motor by testing different pwm values

static char TAG[] = "MOTORS";

MotorController::MotorController(
                                const MotorConfig& mA,
                                const MotorConfig& mB,
                                const MotorConfig& mC,
                                int num_wheels,
                                float wheel_radius_m,
                                float gear_ratio,
                                float max_motor_rpm,
                                float min_motor_rpm)
    : num_wheels_(num_wheels),
      r_(wheel_radius_m),
      D_(gear_ratio),
      max_motor_rpm_(max_motor_rpm),
      min_motor_rpm_(min_motor_rpm)
{
    motors_[0] = mA;
    motors_[1] = mB;
    motors_[2] = mC;
}

esp_err_t MotorController::start()
{
    esp_err_t ret = 0;

    setPWM(M_SLEEP, 4096, 0); // wake up motor controllers
    if (ret == ESP_ERR_TIMEOUT)
    {
        printf("MotorController::start: I2C timeout\n");
    }
    return ret;
}

esp_err_t MotorController::brake()
   {
        esp_err_t ret = 0;

        for (int i = 0; i < num_wheels_; i++) {
            setPWM(motors_[i].in1, 4096, 0);
            setPWM(motors_[i].in2, 4096, 0);
        }
        if (ret == ESP_ERR_TIMEOUT)
        {
            printf("MotorController::brake: I2C timeout\n");
        }
        return ret;
   }

   esp_err_t MotorController::setRPMs(const double* rpms)
   {
        esp_err_t ret = 0;

        for (int i = 0; i < num_wheels_; i++) {
            float rpm = rpms[i];
            // Clamp RPM to min/max
            if (rpm > max_motor_rpm_) rpm = max_motor_rpm_;
            if (rpm < min_motor_rpm_) rpm = min_motor_rpm_;

            if (fabs(rpm) <= deadband_rpm_) {
                ESP_LOGI(TAG, "Motor %d: RPM: %.2f is within deadband", i, rpm);
                // Within deadband, stop motor
                setPWM(motors_[i].in1, 4096, 0);
                setPWM(motors_[i].in2, 4096, 0);
                // setPWM(M2_IN1, 4096, 0); example
                // setPWM(M2_IN2, 4096, 0);
                continue;
            }

            float pwm = rpm_to_pwm(rpm);
            // Test
            ESP_LOGI(TAG, "Motor %d: RPM: %.2f, PWM: %.2f", i, rpm, pwm);

            if (rpm >= 0) {
                // Forward
                setPWM(motors_[i].in1, 4096, 0);
                setPWM(motors_[i].in2, 0, (uint16_t)pwm);
                // setPWM(M3_IN1, 4096, 0); // forward mode example
                // setPWM(M3_IN2, 0, (int)(4096/speed_factor));
            } else {
                // Backward
                setPWM(motors_[i].in1, 0, (uint16_t)pwm);
                setPWM(motors_[i].in2, 4096, 0);
                // setPWM(M2_IN1, 0, (int)(4096/speed_factor)); // reverse example
                // setPWM(M2_IN2, 4096, 0); // reverse
            }
        }
        
        if(ret == ESP_ERR_TIMEOUT)
        {
            printf("MotorController::setRPMs: I2C timeout\n");
            brake();
        }
        return ret;
   }

esp_err_t MotorController::setWheelVelocities(const double* w)
{
    double rpms[NUM_WHEELS] = {0};
    wheel_radps_to_motor_rpm(w, D_, rpms);
    return setRPMs(rpms);
}

void MotorController::wheel_radps_to_motor_rpm(const double* omega_vec_rad_s, double D, double* motor_rpm)
{
    // omega_vec_rad_s: iterable of 3 wheel angular speeds in rad/s
    double factor = (60.0 / (2.0 * M_PI)) * D;
    for (int i = 0; i < 3; i++) {
        motor_rpm[i] = omega_vec_rad_s[i] * factor;
    }
}

double MotorController::rpm_to_pwm(double rpm)
{
    // Convert RPM to PWM value
    double pwm = rpm_to_pwm_scale_ - ((fabs(rpm) / max_motor_rpm_) * rpm_to_pwm_scale_);
    return pwm;
}

void MotorController::testMotors()
{
    const uint16_t test_pwm[] = {0, 100, 255, 380, 476, 504, 816, 1146, 1520, 1854, 2460, 2755, 3265, 3981};
    int test_duration_ms = 500;
    int motor_index = 2; // Test motor 0 (M1)
    for (size_t i = 0; i < sizeof(test_pwm) / sizeof(test_pwm[0]); i++) {
        ESP_LOGI(TAG, "Testing motor %d at PWM %d for %d ms", motor_index, test_pwm[i], test_duration_ms);
        setPWM(motors_[motor_index].in1, 4096, 0);
        setPWM(motors_[motor_index].in2, 0, test_pwm[i]);
        vTaskDelay(pdMS_TO_TICKS(test_duration_ms));
    }
    brake();
    ESP_LOGI(TAG, "Motor %d test complete, stopped motor.", motor_index);
}

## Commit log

2024-09-17 Uploaded the raw Ver0 of the project: CAD and KiCad files.
    [AO3400A--3DModel-STEP-269445.STEP, Arducam Camera OV2640 v6.step, Board Outline.dxf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]
2024-09-18 Fixed silkscreen, modified PCB design, complied with DRC.
    [Mad_Bot.kicad_pcb]
2024-09-19 Fixed mistake in battery bypass circuit.
    [Mad_Bot.kicad_pcb, controller.kicad_sch, drive.kicad_sch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]
2024-09-20 Added Gerber files belonging to the release.
2024-09-20 Rerouted part of the board containing 3.3v regulator and USB connectivity. Routed 90ohm diff pair controlled-impedance traces for USB 2.0 Full Speed.
    [Mad_Bot.kicad_pcb, controller.kicad_sch]
2024-10-14 Updated hardware issues found after first-stage assembly.
2025-11-02 Updated software dependencies. Added raw motor control code.
2025-11-27 feat: Added updated fusion design, software joystick code, URDF model. Updated README.
    [Arducam Camera OV2640 v6.step, Component101.stl, Component105.stl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]
